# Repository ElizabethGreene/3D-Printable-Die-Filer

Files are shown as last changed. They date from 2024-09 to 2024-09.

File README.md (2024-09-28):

# 3D-Printable-Die-Filer

An open source 3d printable die filer v1.0.1

A die filer is a very old tool that uses an external power source to create reciprocating motion for a file.  This allows material removal that is faster and more controlled than hand filing.  It can remove material similar to Side Milling or Slot Milling in a milling machine.  Additionally, when equipped with square or triangular file, it can file a sharp corner e.g. for keyways or gear teeth.

This is an early release, and while the tool is functional, it is *not* a production quality tool.  It will cut metal.  A demo video in the images folder shows it cutting brass, and I successfully filed a keyway in a steel gear with it.  There is room for improvement, and feedback is welcome, positive or negative via the github issues tracker at <https://github.com/ElizabethGreene/3D-Printable-Die-Filer>

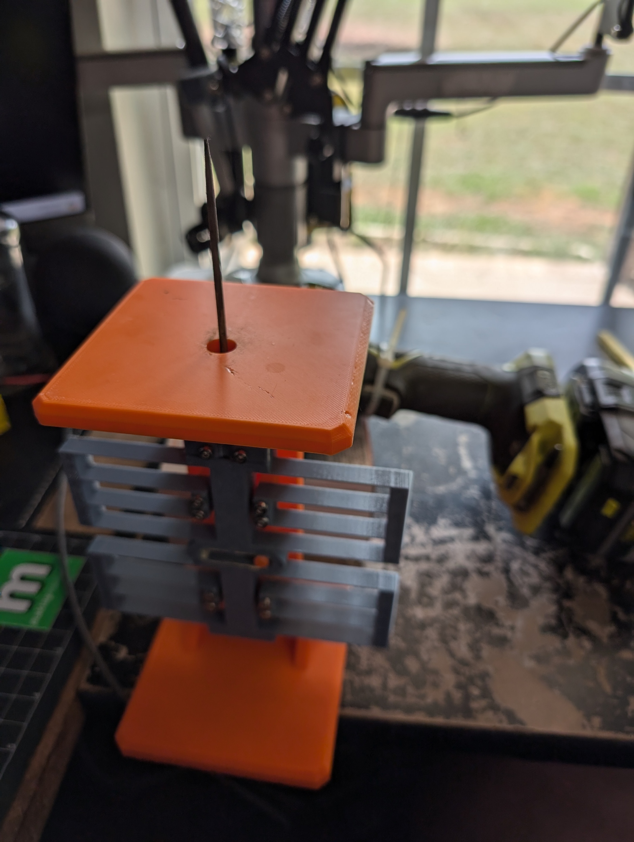
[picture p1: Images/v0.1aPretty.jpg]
Glamour Shot image


## Danger

 There is a pinch hazard between the bottom of the flexure and the base.  It **hurts**.  Additionally, there are many pinch points for smaller fingers, so it should not be used by or around small children. These should be covered or corrected in future development. While this tool is "only" plastic, it can still cause painful injuries. Safety glasses are highly recommended when using any tool, including this one.

## Features

This was specifically designed to use as few "vitamins", non-printed components,  as possible.  This is accomplished with a compliant mechanism for the linear stage, and using a drill as the power source.  The only hardware required to assemble it are M3 screws, nuts, a washer, and one 608z skate bearing.

## Bill of Materials

* 3D Printed Parts
* M3 Hardware
  * All M3 hardware are standard DIN 912 socket head cap screws.
  * I use this Iexcell M3 screw assortment kit from Amazon. <https://amzn.to/3B85y6H>
  * 4 M3x30mm Socket Head Cap screws - Flexure to Support Mount screws
    * TODO: These can be shorter.
  * 8 M3x14mm Socket Head Cap screws - Base to Support and Worktable to Support Mount screws
  * 1 M3x30mm Socket Head Cap screw - Crankshaft/eccentric reinforcement
  * 2 M3x12mm Socket Head Cap screw for File Clamp
  * 1 M3x5mm Socket Head Cap screw - Bearing Retainer
  * TODO: 2 as-yet unknown length M3x?? screws for tilt table mechanism.
  * 1 M3 washer - Bearing Retainer
  * 1 608z Skate Bearing
  * 8 M3 nuts
* White Lithium Grease
  * I used "Sta-Lube Multi-Purpose Super White Lithium Grease"
* Files (See Below)

## Files

The file holder is designed to accommodate a variety of different files with shaft diameters from 1/4" to 1/8", down to 2.8mm.

* Harbor Freight "Pittsburgh Needle File Set" or "Central Forge Precision Needle file Set" both work.
* Commercial Die filer files (obsolete and very rare) have a 1/4" round shank and will work.
* Larger files can be made to work by grinding the shank to fit.
* Some files may require enlarging the hole in the work surface

## Assembly

### Reference Photos

Front:
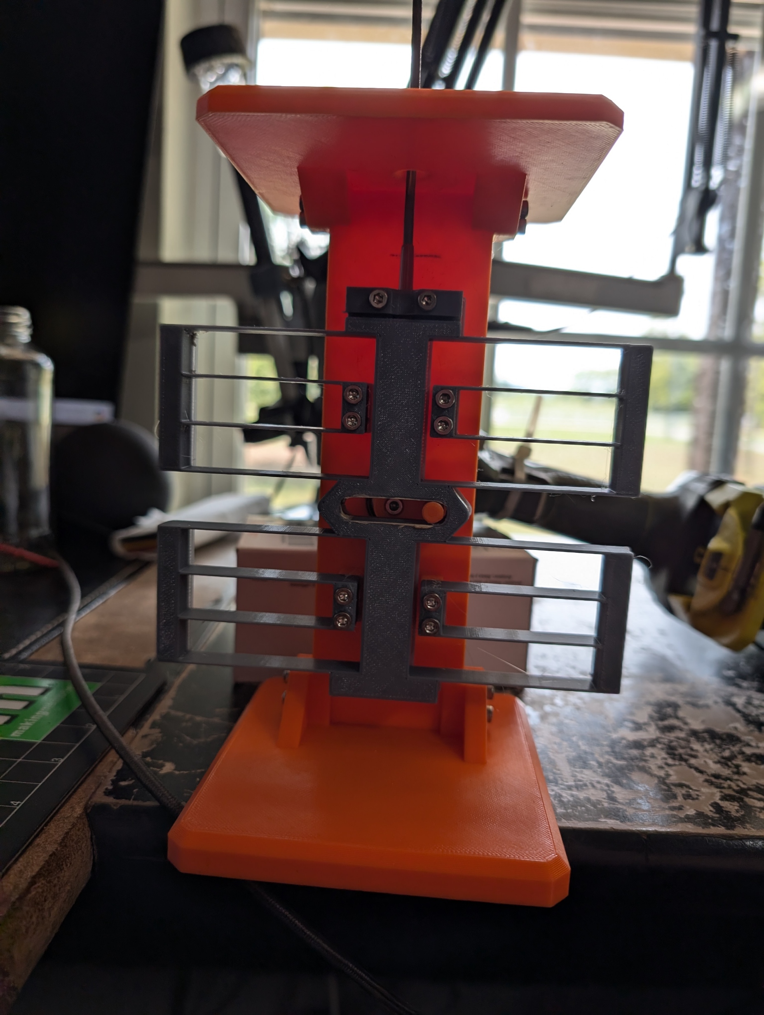
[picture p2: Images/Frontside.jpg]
Front


Back:
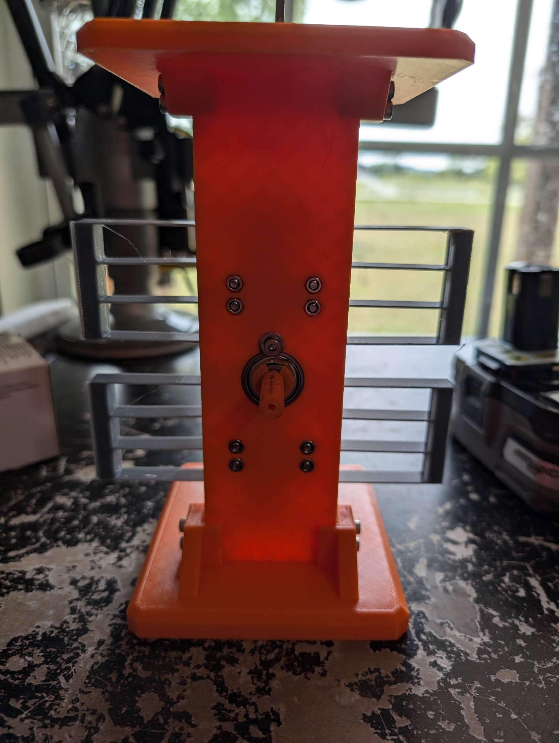
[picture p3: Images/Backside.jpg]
Back


Crank in Flexure Slot
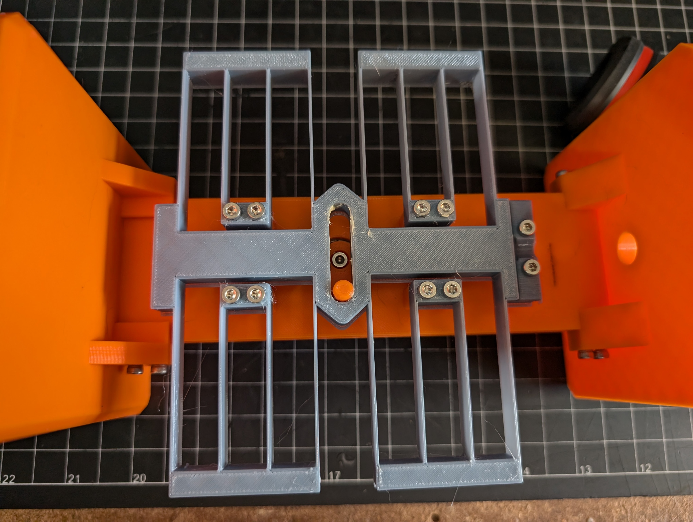
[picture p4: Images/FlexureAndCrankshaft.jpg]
Crank in Flexure Slot


### Printing

* Print all parts in the orientations shown in the picture below.
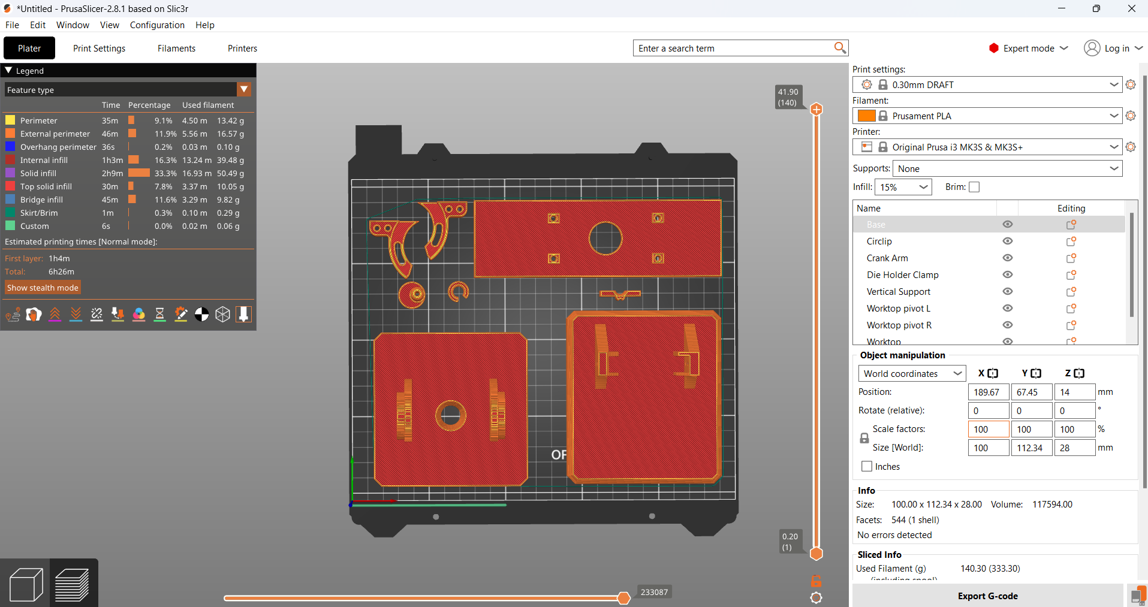
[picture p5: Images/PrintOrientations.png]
Print Orientations

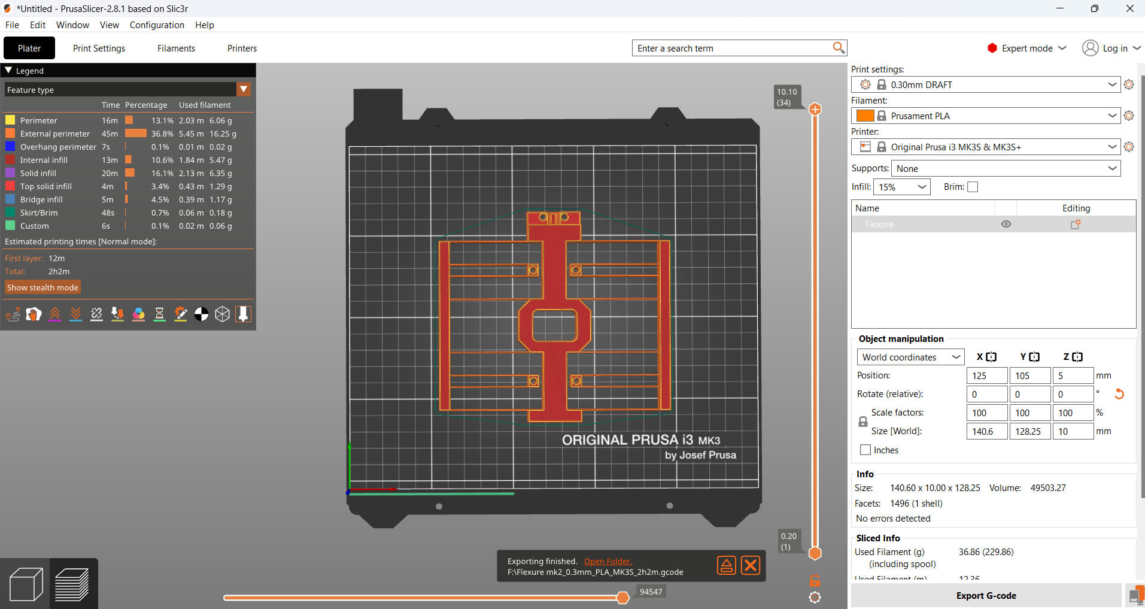
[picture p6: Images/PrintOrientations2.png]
Print Orientations 2

  * Note that one side of the C-shaped Circlip has a chamfer.  The flat side should rest on the print bed.
  * The Tilt Table 1.0.1 test model was printed in Hatchbox PLA on a Prusa Mk3S using the Draft 0.3mm preset
    * The Flexure on the original model was printed in Hatchbox PETG and tested extensively (30+ hours)
    * The tilt table's modified flexure in PLA has not been as extensively tested and is considered experimental.

### Step-by-Step Assembly

* Bearing
  * Press the bearing into the support
  * Secure the bearing in the support with a M3x5mm screw and washer
* Crankshaft/Eccentric
  * Place the crankshaft through the bearing, and secure with the circular clip (circlip)
    * Note, the circlip groove is chamfered to enable printing.  The angle in the circlip needs to match this chamfer.
    * A large pair of pliers is helpful installing this clip
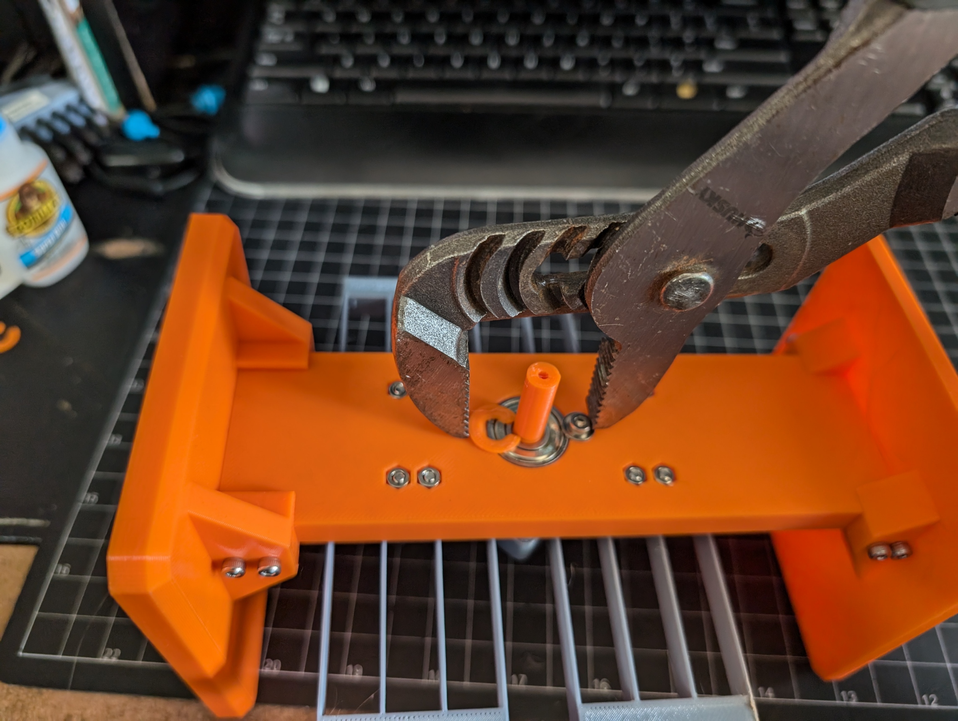
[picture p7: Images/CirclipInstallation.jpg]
Circlip Installation

    * Drive an M3x30mm screw fully into the crankshaft from the front side
    * This screw reinforces the crankshaft to help prevent failure between layers.
    * This screw slightly expands the shaft, so it needs to be installed *after* the shaft is installed in the bearing.
* Base
  * Attach the base to the support with 4 M3x14mm screws
    * The shortest side of the base faces toward the rear, the side that has the circlip and bearing retainer screw.
* Tilt Table Supports
  * Attach L and R Tilt table supports to vertical support with 2 M3x15 SHCS in each side.  
* Worktop
  * Press two M3 nuts into Worktop underside
  * Place Worktop supports into tilt table support
  * Secure with 2 M3x14mm screws
    * The shortest side of the worktop faces toward the rear, the side that has the circlip and bearing retainer screw.
* File Holder clamp
  * Press in two M3 nuts into the back of the Flexure.  This is a tight fit, and pliers may help.
  * Attach the file holder clamp to the flexure with 2 M3x12mm screws.
  * The file holder clamp is reversible.
    * For large shank files, the concave side should face the flexure.
    * For small shank files, the convex side should face the flexure.
* Flexure
  * Using 4 M3x30mm screws and nuts, attach the flexure to the support.
  * The file holder clamp should facing forward/out so they are easily removable to change files.
  * The crankshaft eccentric should engage the hole in the flexure.
* Lubrication
  * Apply a small dot of grease in the eccentric hole in the flexure.

## Usage

* Install a file.
  * Loosening the File clamp screws.
  * Insert file into the hole.
  * If necessary, flip the file clamp so can grasp securely.
  * Tighten the File Clamp screws.
* Grip the crankshaft with the chuck of a drill.
  * Optional and highly recommended, support the drill so the weight isn't hanging on the crankshaft.
* Optional, clamp the base to a worksurface.
* Using a zip-tie or clamp, turn on the drill.
* Press the work into the moving file.

## Note

 A high pitched chirping sound when cutting is called chatter and generally means you are pressing too hard.

## Changelog

* 0.0.1 alpha - Initial release
* 0.0.2 alpha - Bugfix: Bore and Counterbore in crankshaft missing
* 1.0.1 - Branch: Tilt Table
  * Iterate major version number
    * All printable components (except the Circlip) have been modified and are incompatible with previous release
  * Added tiltable table mechanism
  * Reinforced vertical flexure mechanism to reduce deflection
  * Replaced the fragile glue-together crank-and-pin mechanism with a significantly stronger eccentric cam mechanism
  * Simplified model
    * Removing unneeded washers
    * Combined bearing components
    * Updated model joints for simulation
    * Removed redundant screws in flexure mechanism
  * TODO:
    * Test print
    * Endurance test for PLA flexure
    * Update BOM
    * Make video about making files
    * Update screw lengths for flexure to vertical support
    * Knob for tilt table screws?
    * Update Photos in readme
      * Front
      * Back
      * Circlip
      * Flexure
      * ~~Print Orientations~~

## Problems/disadvantages and Opportunities for future work

* There are pinch hazards as mentioned in the Danger section.
* The flexure is insufficiently stiff against off-axis forces. Machine filing uses low tool pressure, so it's still usable, but I'd like it to be stiffer.
* The base and worktable can flex under heavy workpieces.
* Supporting the drill works, but is dodgy. A better way to mount that is critical.
* A zip-tie to hold down the drill trigger works, but is dodgy. A clamp would be a better solution.
  * Forking the design to use a dedicated motor merits consideration
* Increase the overall stroke length from 25mm to 35-40
* Adapt an adjustable stroke length mechanism ex: <https://youtube.com/shorts/UjDqezJ2Gh0?si=csQhwm905_5Tf_nh>
* ~~Increase the flexure linear throw~~ and consider pre-stressing at assembly to reduce the inherent stiffness at the center position.
* Add an overarm support
  * A good overarm support would allow the unit to be used as a scroll saw, an extremely useful tool.
  * A good overarm support would also allow using it as a power hacksaw for thinner stock
* Add work hold-downs
* Consider forking and stretching the design for a big power hacksaw
* ~~Edit this documentation to include pictures.~~
* ~~A tilting worktable would be nice.~~

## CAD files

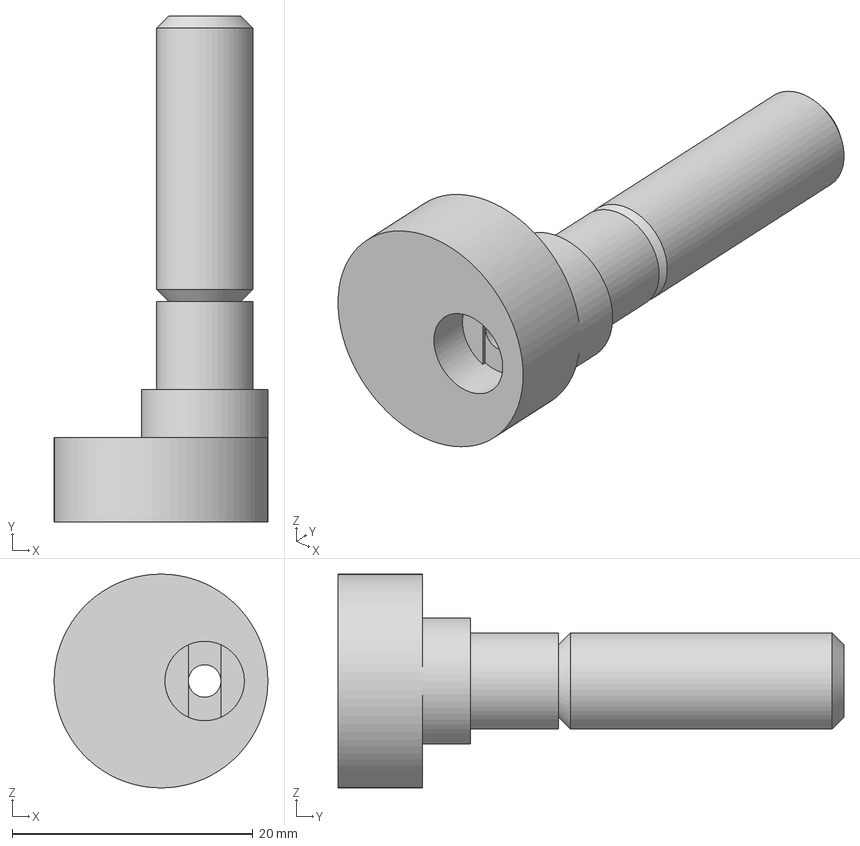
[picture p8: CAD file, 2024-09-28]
3mf/Crank Arm.3mf
17.8 x 42.0 x 17.8 mm

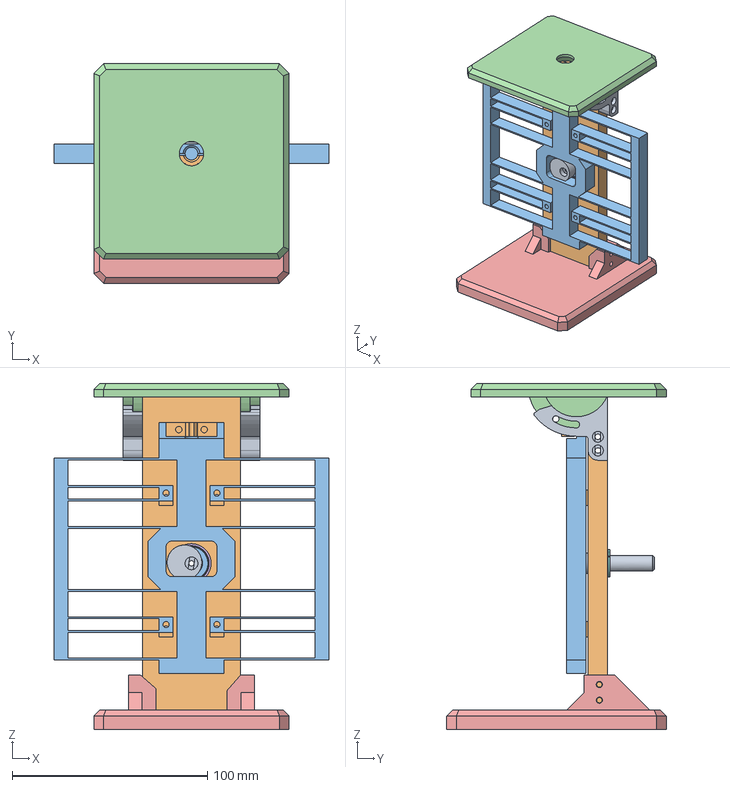
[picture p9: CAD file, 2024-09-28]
Die Filing Machine.step
140.6 x 112.3 x 177.0 mm
Worktop pivot L
Worktop pivot R
5972K501_Ball Bearing
Circlip
Die Holder Clamp
Worktop
Base

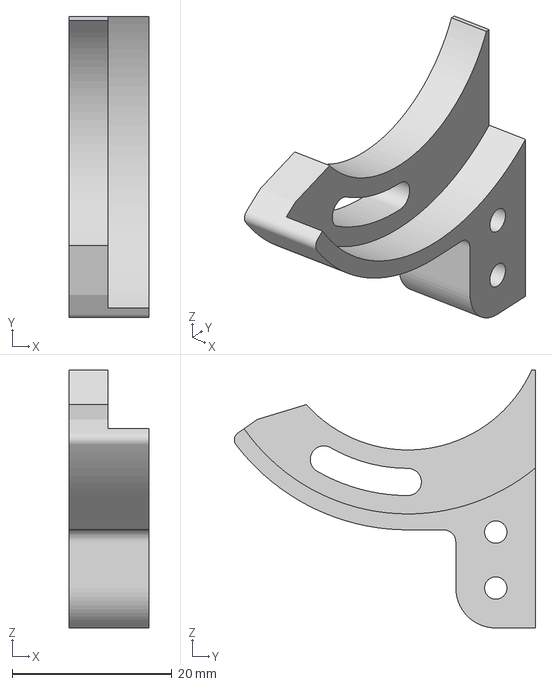
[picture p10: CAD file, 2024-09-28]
3mf/Worktop pivot L.3mf
10.0 x 37.7 x 32.3 mm

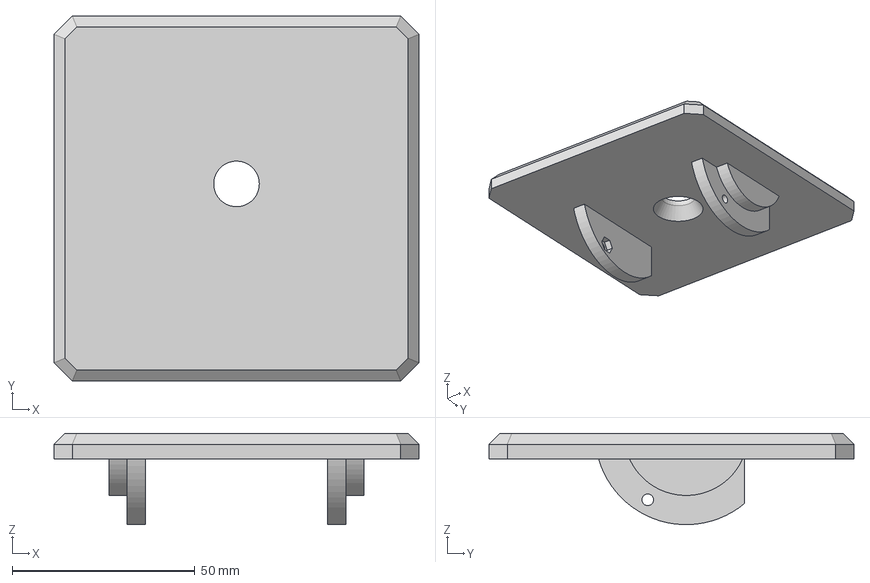
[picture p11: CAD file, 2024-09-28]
3mf/Worktop.3mf
100.0 x 100.0 x 25.0 mm

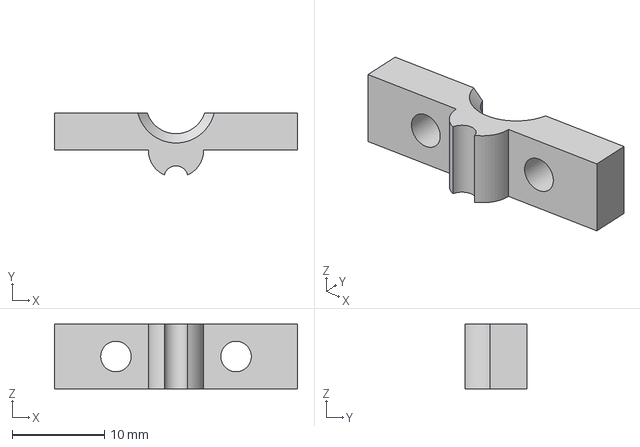
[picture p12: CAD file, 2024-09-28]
3mf/Die Holder Clamp.3mf
26.3 x 6.73 x 7.00 mm

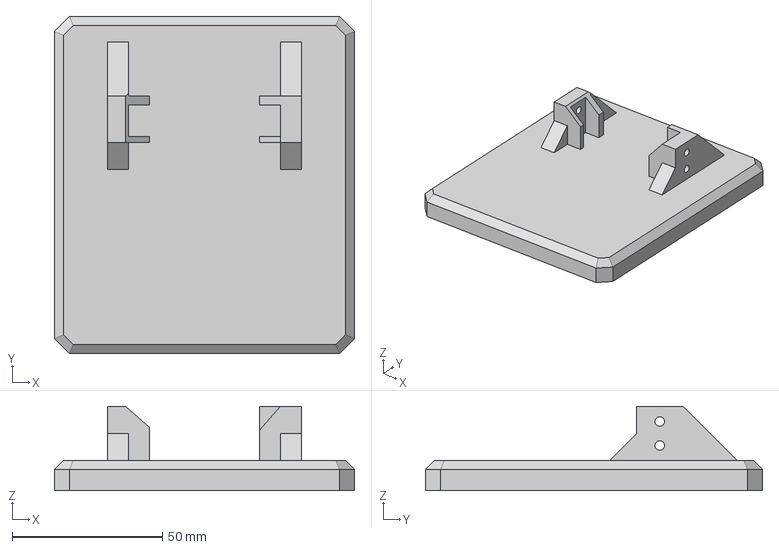
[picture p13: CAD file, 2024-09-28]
3mf/Base.3mf
100.0 x 112.3 x 28.0 mm

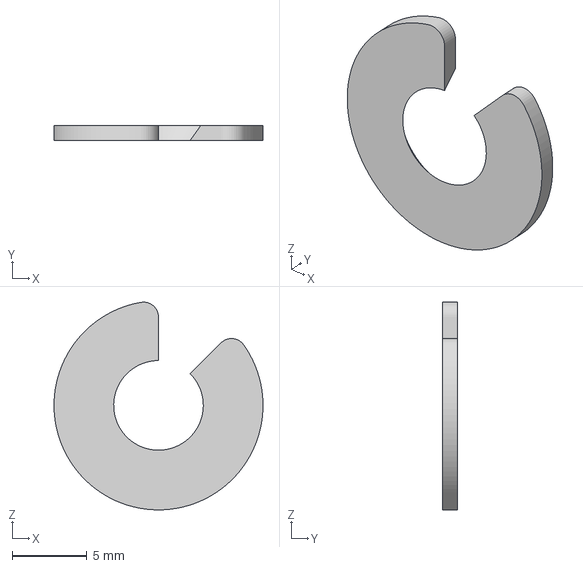
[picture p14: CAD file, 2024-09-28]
3mf/Circlip.3mf
14.0 x 1.00 x 13.9 mm

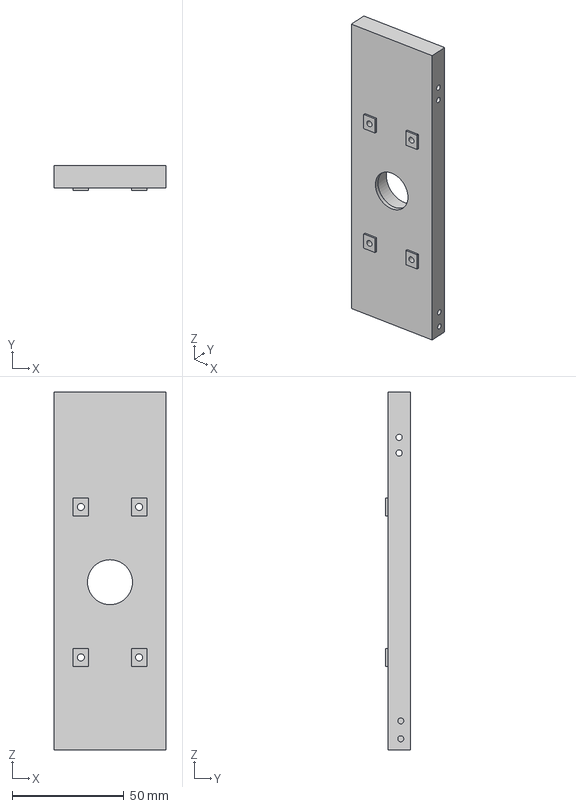
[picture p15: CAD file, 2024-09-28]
3mf/Vertical Support.3mf
50.0 x 11.0 x 160.0 mm

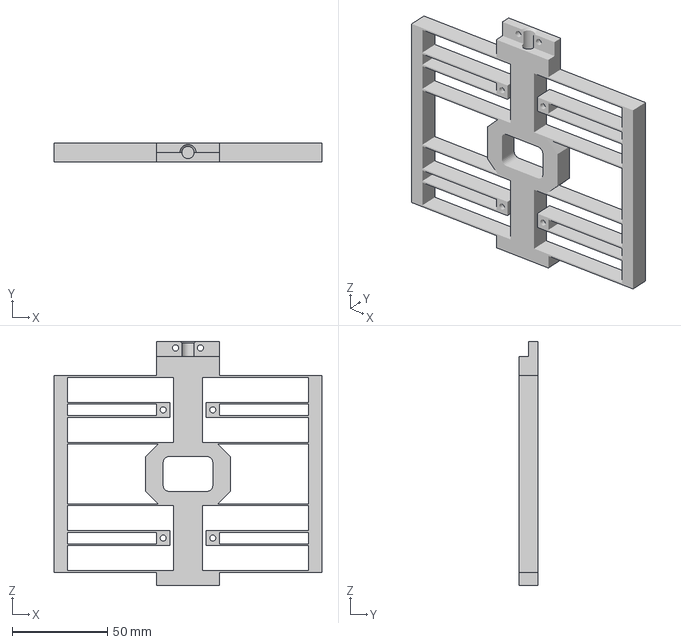
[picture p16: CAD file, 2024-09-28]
3mf/Flexure.3mf
140.6 x 10.0 x 128.2 mm

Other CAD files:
3mf/Worktop pivot R.3mf
Die Filing Machine.f3d
stl/Base.stl
stl/Circlip.stl
stl/Crank Arm.stl
stl/Die Holder Clamp.stl
stl/Flexure.stl
stl/Vertical Support.stl
stl/Worktop pivot L.stl
stl/Worktop pivot R.stl
stl/Worktop.stl

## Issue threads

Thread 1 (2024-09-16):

Build Log & Feedback

showerst, 2024-09-16:
Thanks for the design! This was great and pretty easy to build. Feedback:

1. I printed all parts on a Bambu A1 out of PLA, a mix of eSun and Bambu. The fitment was great, and the flexure surprisingly seems OK, time will tell if PLA will work for that long term.
2. I drilled out the crank pin with a #41 drill to fit the M3 screw, then drilled a small countersink for the head using a larger bit. Ideally there would be an M3 tapping-sized hole (2.5mm?) and a countersink in the model, the screw should self-tap fine.
3. On my build, the back of some of the files is super close to the back of the hole in the table, so it files away a bit of the table on some strokes. A larger table hole would be good.
4. I snapped off my first crankshaft because I held the drill at too much of an angle, an alternative crank shaft design with a hole for a 6mm metal rod and a retaining screw would be cool.
5. This runs surprisingly smoothly, I'm thinking of fitting it to a cheap sewing machine motor with a foot petal if I can find one that's low-speed enough.
6. I bought these [cheap files on amazon](https://www.amazon.com/dp/B07TXXB1MG) and they work fine.

ElizabethGreene, 2024-09-16:
Thanks for the feedback.

I have a branch with a tilting table mechanism that also increases the
stiffness of the mechanism pretty significantly that I've been working on.
I'll double-check the alignment between the file and the hole in the deck.

The sewing machine motor is an excellent idea, and I too split
a crankshaft.  The drill power system really is a problem. I was trying to
keep the part count as low as possible, but I think that's a step too far.
I'll work on it.

Do you need a pulley to connect up the sewing machine motor?  If so, I can
pop one out tonight.

Elizabeth Greene
615-280-0830

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

ElizabethGreene, 2024-09-17:
Created issue #2 for crankshaft not including the hole and counterbore for the axial reinforcement screw.

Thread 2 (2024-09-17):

0.1 alpha does not include updated crankshaft with hole and countersink for axial reinforcement screw

ElizabethGreene, 2024-09-17:
0.1 alpha does not include updated crankshaft with hole and countersink for axial reinforcement screw.  Not sure what happened here, it's in the durability test artifact, but not in the Fusion project or output folder.  The attached .gcode renamed to .txt file has it, and can be used for reference geometry.

[Uploading Crankshaft Pin Circlip_0.3mm_PLA_MK3S_26m.txt…]()

ElizabethGreene, 2024-09-19:
Fixed with Commit 2d1605dadf33b9d38a91cf5c45b4a9081d88ee2a

Closed 2024-09-19.

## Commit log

2024-09-12 Create Die Filing Machine v11.step
    [Die Filing Machine v11.step]
2024-09-19 Fixing Issue #2 = 0.0.2a
    Re-added Crankshaft reinforcement bore and counterbore for Issue #2
    Bumped version # to 0.0.2a
    Added Lint plugin for Readme.md
    Fixed Lint issues in Readme.md
    [Crankshaft.3mf, Crankshaft.stl, Die Filing Machine.f3d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]
2024-09-19 Removing old .f3d/step, moving STL to STL folder
    [Crankshaft.stl, Die Filing Machine v11.f3d, Die Filing Machine v11.step]
2024-09-23 Update Die Filing Machine.f3d
    Added tilt table initial rev. This won't work; the layer lines between the worktable and vertical support will interlock instead of sliding contact. Need to rev this with the vertical support mounts printed horizontally. Bonus points if they mount in the same holes as the original table mount.
    [Die Filing Machine.f3d]
2024-09-24 Tilt table progress
    * 0.1.3 alpha - Branch: Tilt Table,
    * removed unneeded washers
    * added tilt table
    * combined bearing components
    * created joints
    * Iterating minor version number as worktop parts are incompatible with previous release
    [Base.3mf, Base.stl, Circlip.3mf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]
2024-09-27 Changed to eccentric drive instead of crank
    Changed to eccentric drive instead of crank
    Reinforced flexure
    Reduced flexure mounting height
    Extended File grip vertically
    Repositioned Bearing
    Reworked Tilt supports for new file position hole
    TODO: Reduce Tilt Support bracket radius
    This commit is UNTESTED, and not recommended for printing
    [Base.3mf, Base.stl, Circlip.3mf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]
2024-09-28 Test printing
    [Base.3mf, Base.stl, Circlip.3mf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]
2024-09-28 Updating readme and print orientations
    Note: new version number will be 1.0.1
2024-09-28 Readme.md No glue! updated version number
